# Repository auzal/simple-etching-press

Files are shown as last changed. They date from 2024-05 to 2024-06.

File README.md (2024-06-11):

# Simple Etching Press

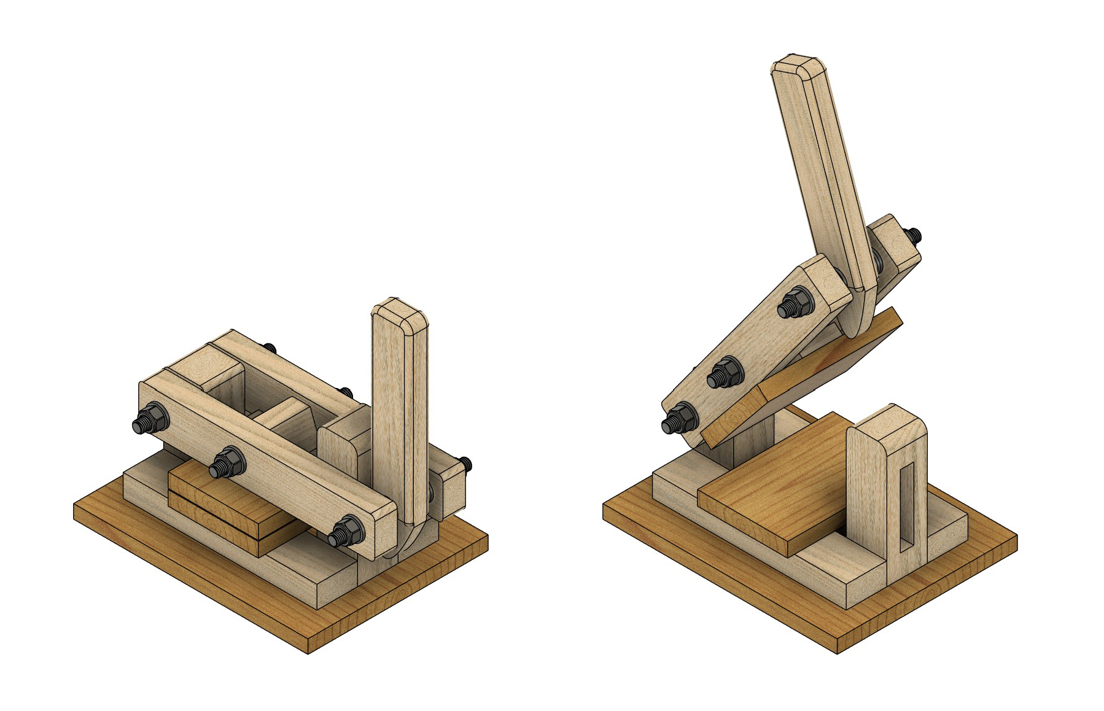
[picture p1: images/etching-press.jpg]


A low cost small format etching press that can be made out of lumber and threaded rods.

Developed with Andrea Juarez and Manuel Rapoport in 2020. 

3D files (Autodesk fusion and .STEP) can be found in the [3dFiles](3dFiles) directory.

# Assembly guide

## Bill of materials

All dimensions expressed in millimeters. Any part marked "(x2)" means that two copies of it are needed.

Many of these dimensions are approximate. The first prototype for this press was made without measuring dimensions, only keeping in mind the size relationship between parts.

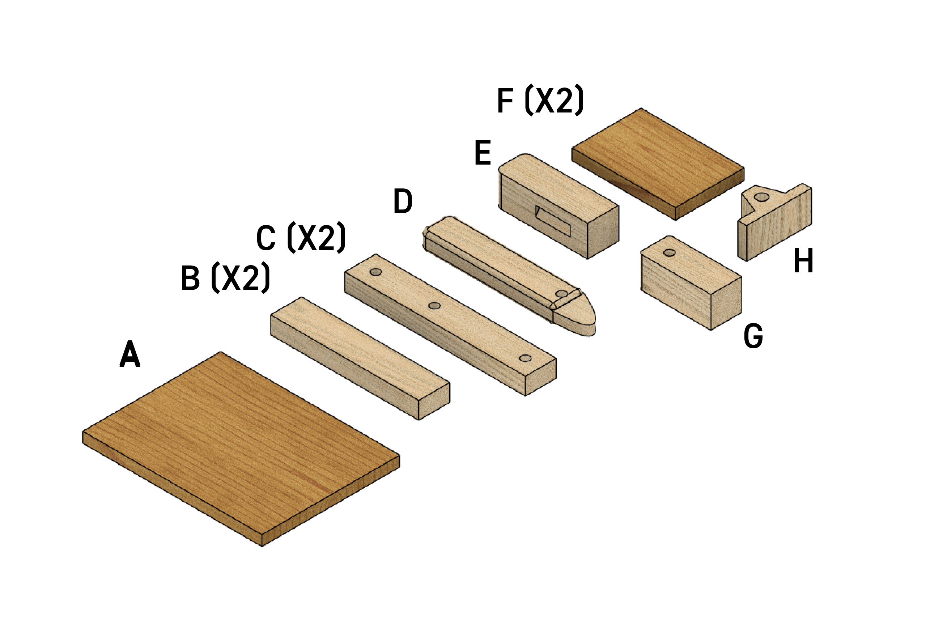
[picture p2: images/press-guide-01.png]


**Plywood or MDF Parts:**

- A - 200 mm x  260 mm x 15 mm
- F (x2) - 100 mm  x 150 mm x 16 mm 

**Hardwood parts (pine or eucalyptus were used for these):**

- B (x2) - 45 mm x  215 mm x 25 mm
- C (x2) - 45 mm x  262 mm x 25 mm (see detailed plan)
- D - 45 mm x 240 mm x 25 mm (see detailed plan)
- E - 45 mm X 135 mm x 45 mm (see detailed plan)
- G - 45 mm x 105 mm x 45 mm (see detailed plan)
- H - 94 mm x 45 mm x 45 mm (see detailed plan)

**Hardware and others**

- 3 x [Steel threaded rod M12 - 150 mm long](https://www.mcmaster.com/93805A647/)
- 6 x [Steel Nylon-Insert Locknut M12](https://www.mcmaster.com/93625A400/)
- 18 x [Steel Washer M12](https://www.mcmaster.com/98687A114/)
- Wood glue
- Sandpaper

## Detailed part plans

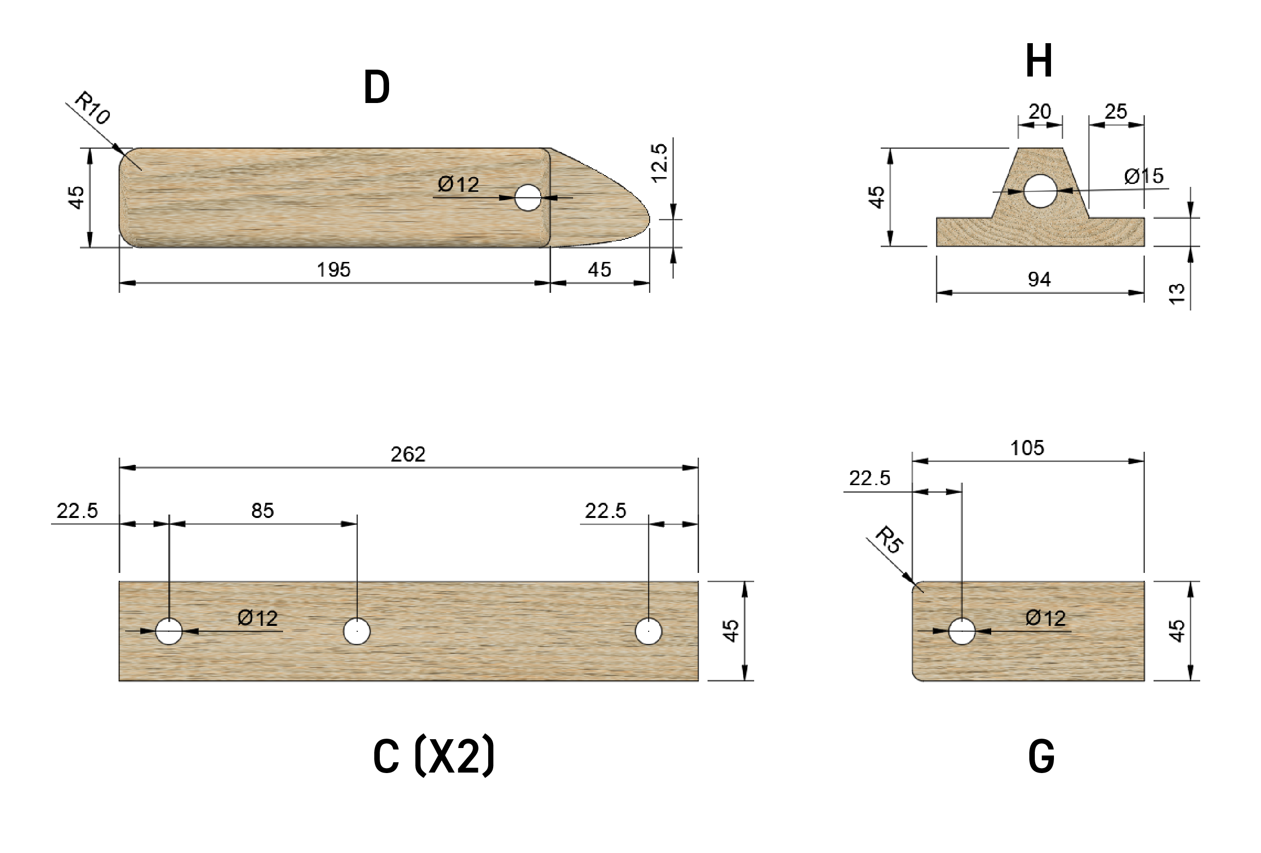
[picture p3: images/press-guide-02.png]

Detail of handle (D), plate pivot (H), arms (C) and arm pivot (g)

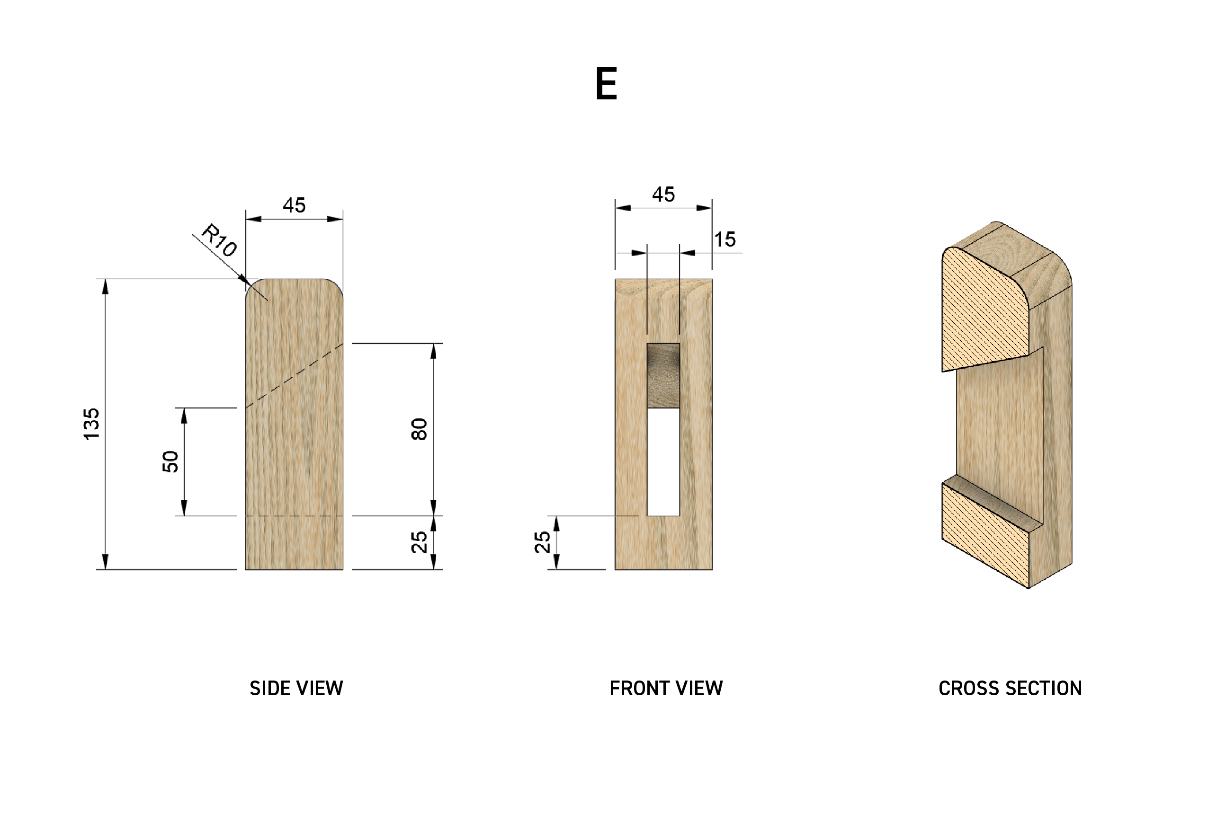
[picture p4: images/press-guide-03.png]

Detail of front lever lock (E)

## Assembly steps

1 - Take base (A) and glue parts B, E and G as shown. These parts can also be secured with flat head wood screws from below. Make sure they are flush to the bottom of the base so that the press can have a level and stable surface to sit on.

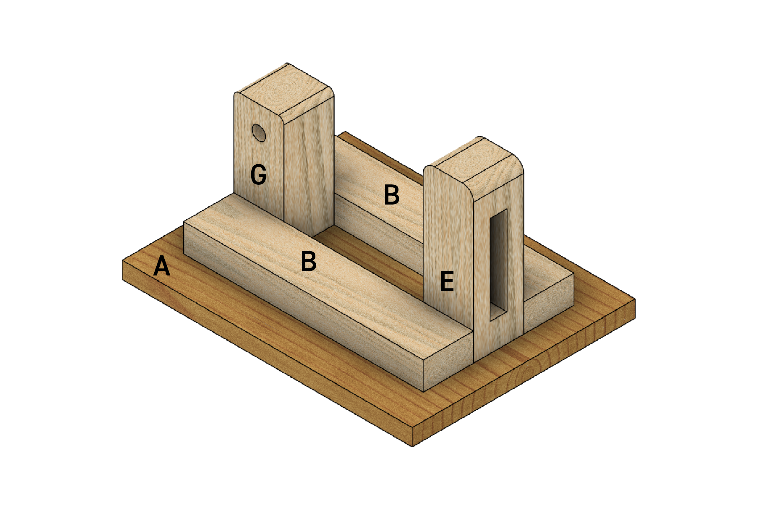
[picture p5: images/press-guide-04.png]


2 - Glue bottom plate (F) to the previous assembly, centered in the space left between parts E and G.

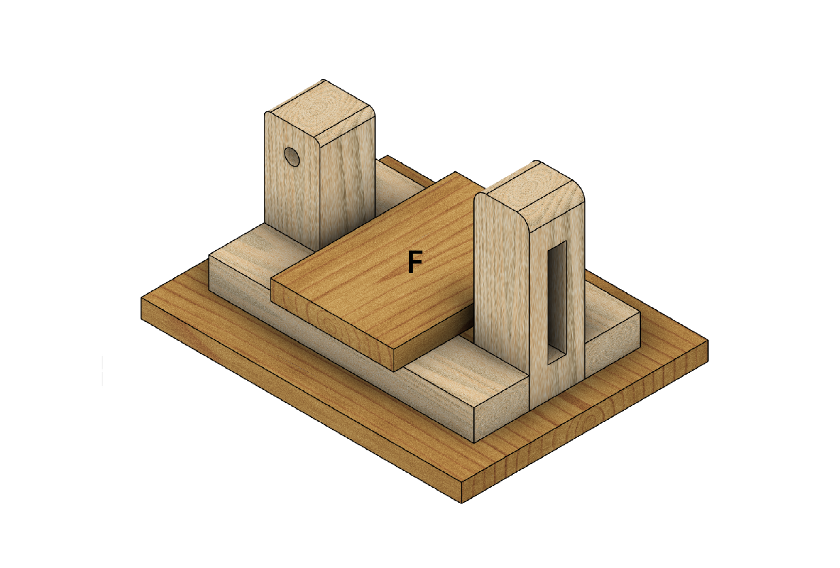
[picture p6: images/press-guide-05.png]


3 - Glue other plate (F) to the pivot piece (H), keeping both parts centered to each other.

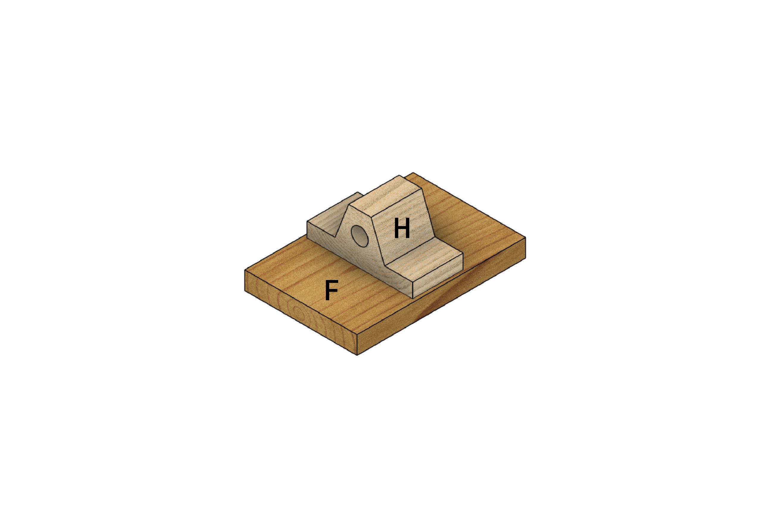
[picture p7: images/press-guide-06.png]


4 - Assemble all parts with the threaded rods, nuts and washers. See detailed view.

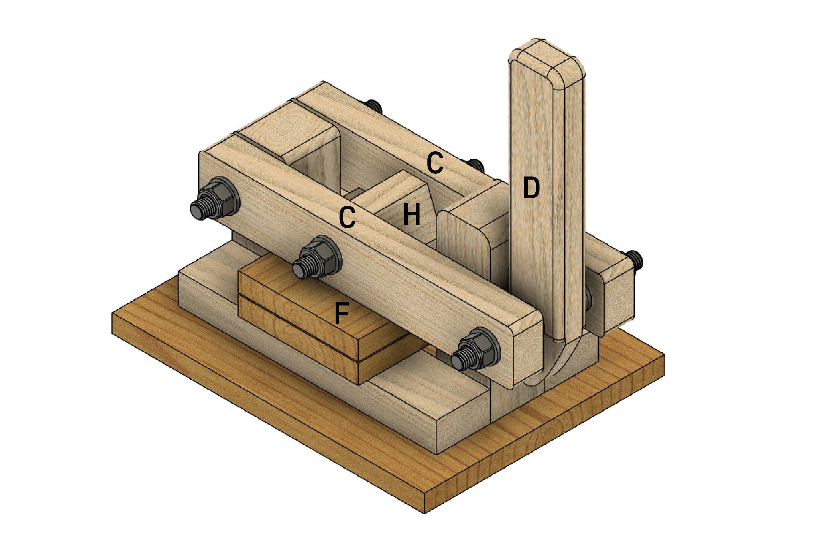
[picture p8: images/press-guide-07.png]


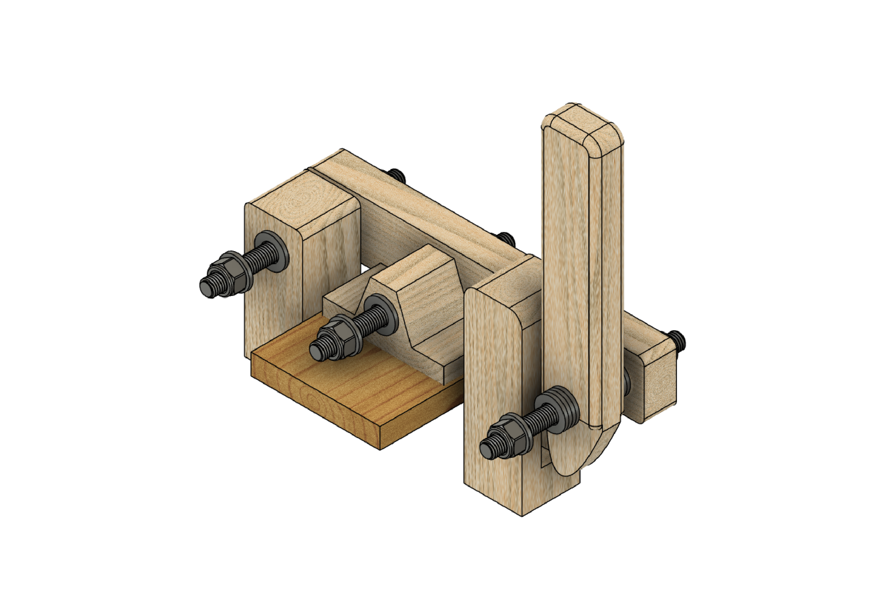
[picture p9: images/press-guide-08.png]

Detailed vew of hardware distribution.

**Notes:**

- The internal faces of the plates (F) need to be as flat as possible. If using plywood, make sure you sand them down before assembling. This will help achieving an even pressure across the plate. 

- The washers used as padding against the handle (D) can be replaced with sections of hose or copper pipe.

# Additional images

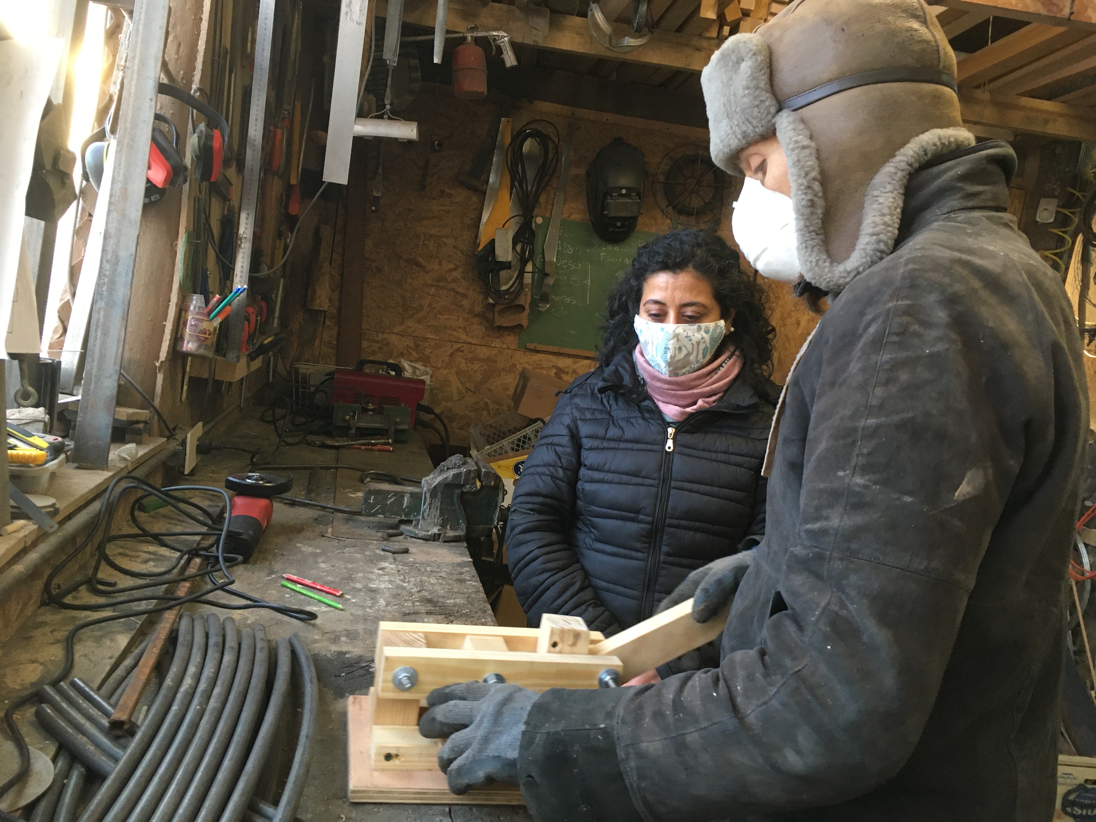
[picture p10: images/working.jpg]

Andrea and manuel working on the first prototype

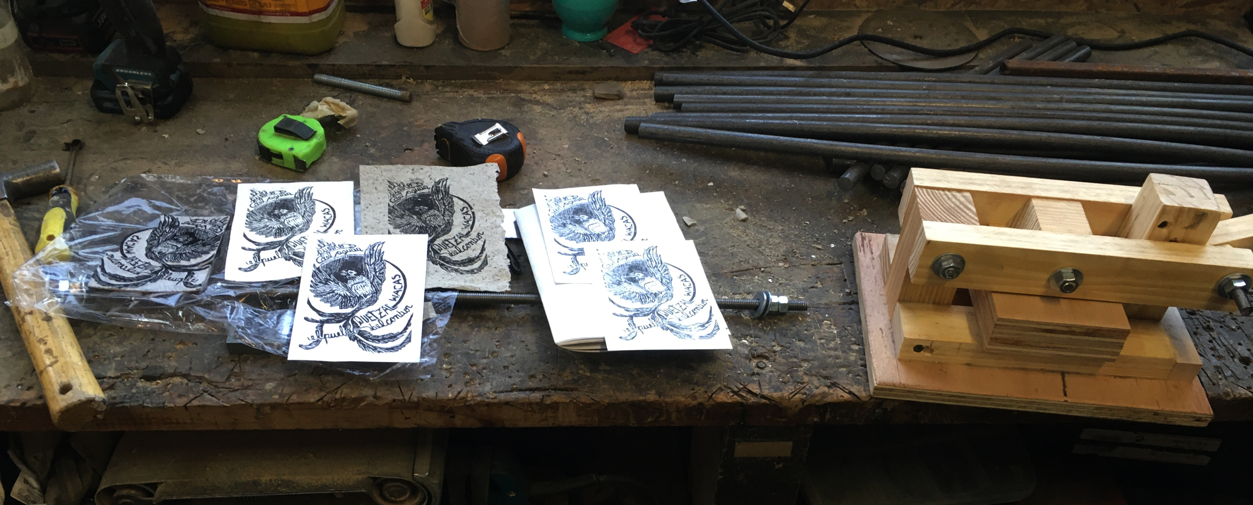
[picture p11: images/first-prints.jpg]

Andrea and manuel working on the first prototype

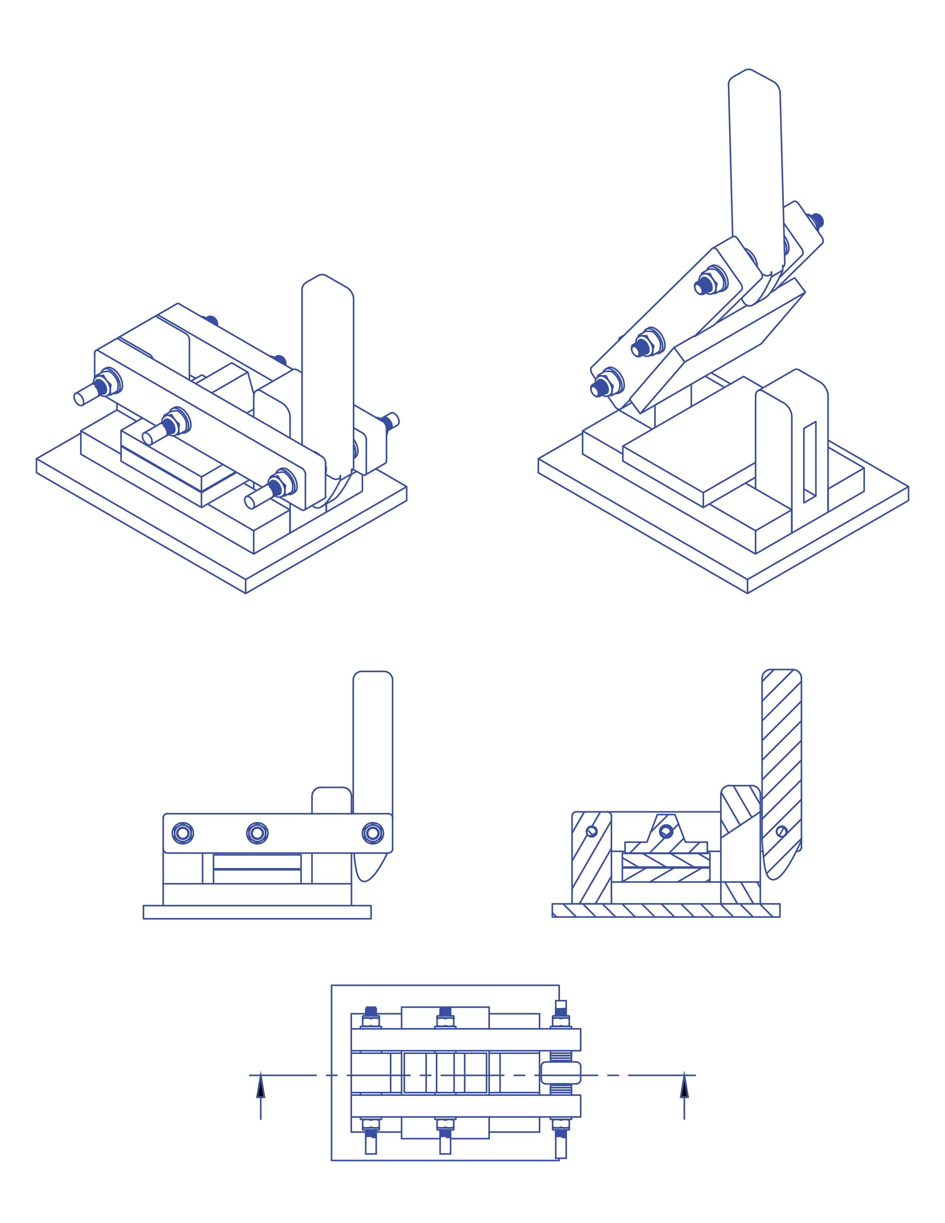
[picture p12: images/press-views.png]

Technical drawing

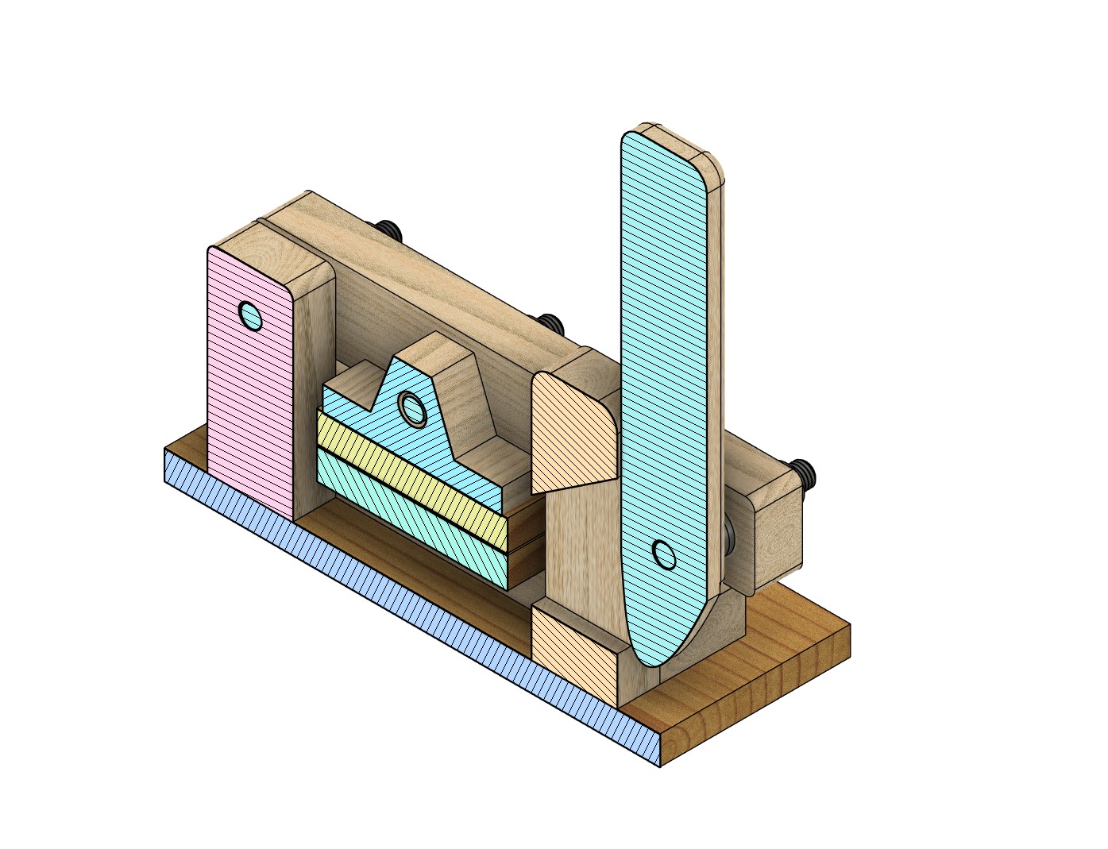
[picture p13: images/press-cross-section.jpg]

Cross-section of the press

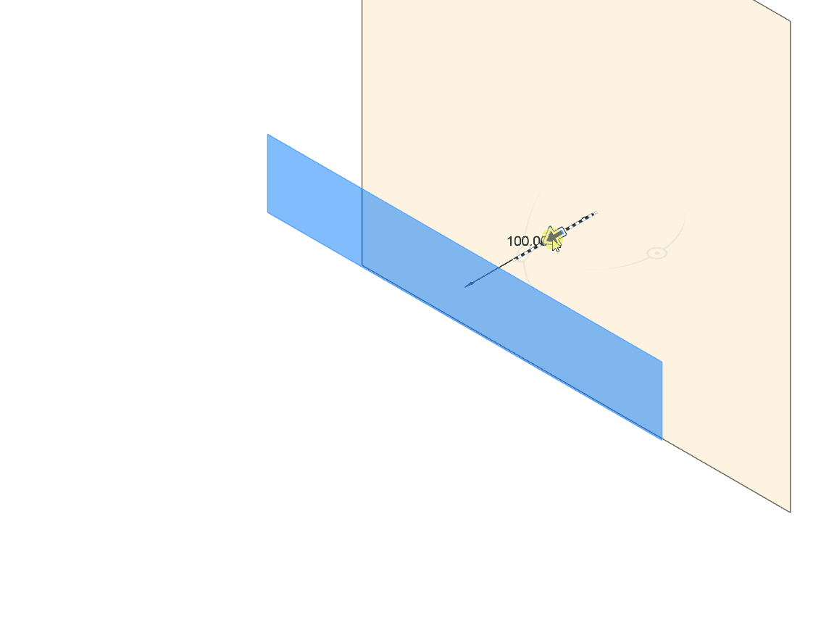
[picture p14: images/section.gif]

Cross-section analysis of the press

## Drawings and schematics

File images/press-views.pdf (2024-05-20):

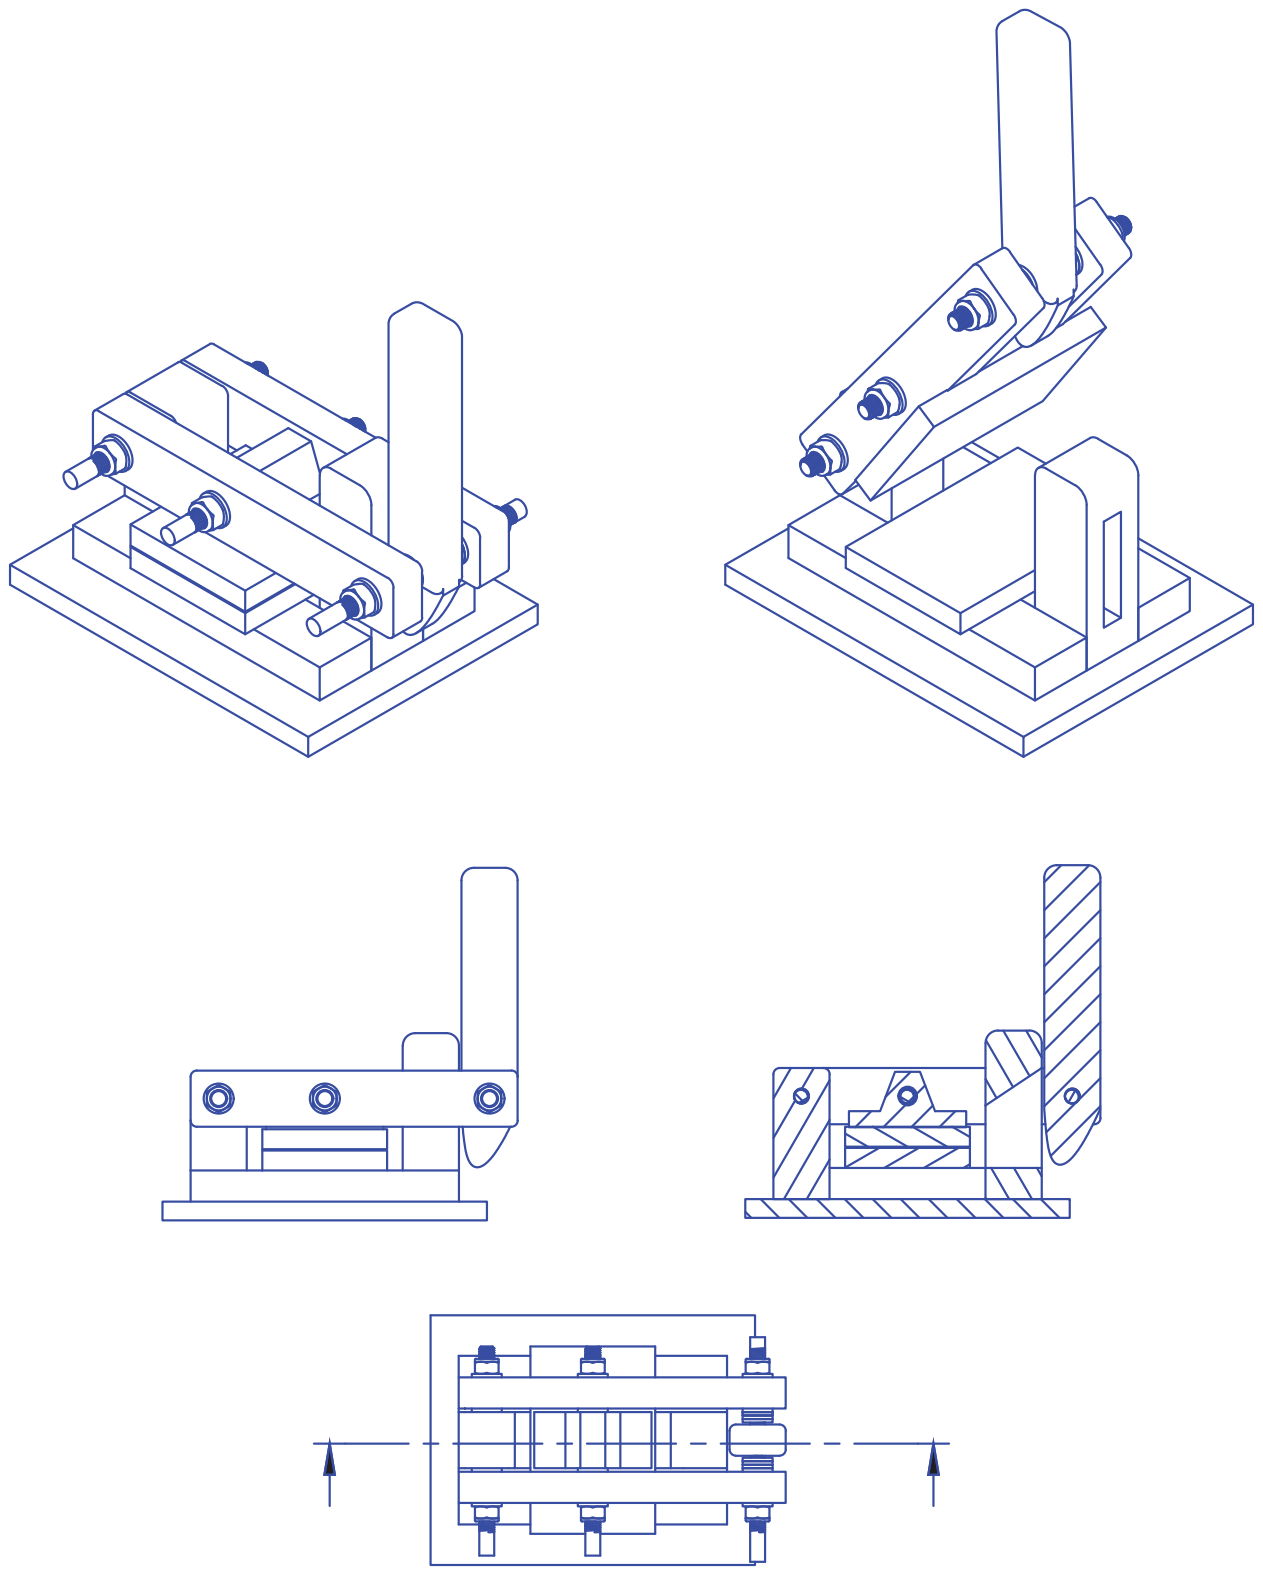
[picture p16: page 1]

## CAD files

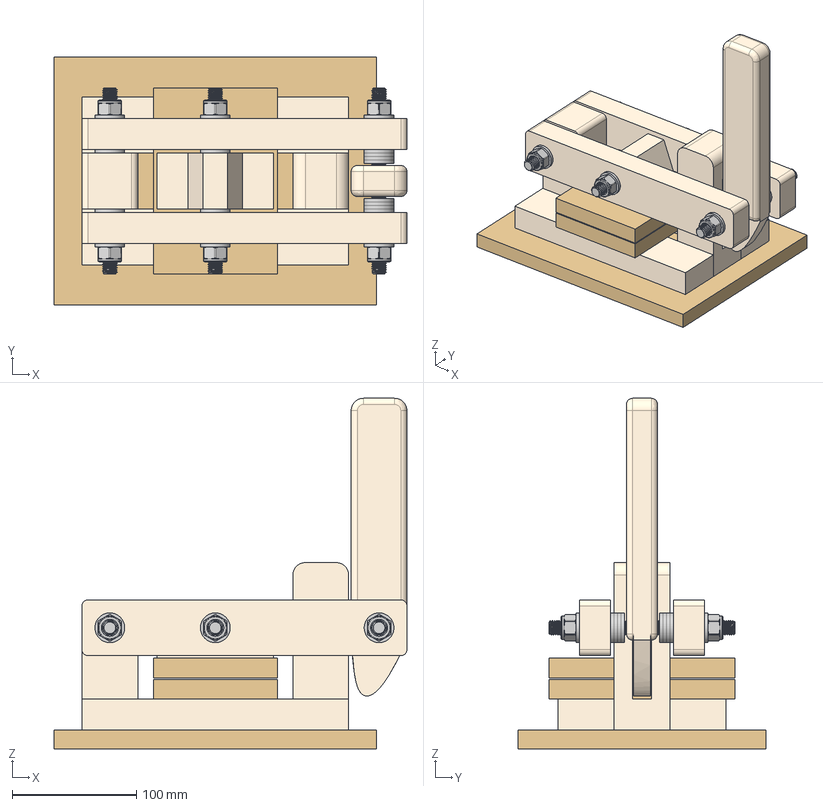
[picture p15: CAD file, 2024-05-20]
3dFiles/etching-press.step
284.5 x 200.0 x 282.5 mm
Handle
Horizontal 1
Base Sheet
Horizontal 2
Vertical block back
Vertical block front
Plate base
Plate top
Plate pivot
Arm 2
Arm 1
93805A647_18-8 Stainless Steel Threaded Rod x 3
98687A114_General Purpose Steel Washer x 10
93625A400_18-8 Stainless Steel Nylon-Insert Locknut x 3
98687A114_General Purpose Steel Washer(Mirror) x 6
93625A400_18-8 Stainless Steel Nylon-Insert Locknut(Mirror) x 3
98687A114_General Purpose Steel Washer(Mirror) (1) x 4

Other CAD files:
3dFiles/etching-press.f3d
